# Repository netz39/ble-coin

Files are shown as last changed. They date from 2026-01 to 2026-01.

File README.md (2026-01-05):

# BLE Keyfob Authentication (PROJECT STATUS: DEPLOYED)
The purpose of this project is to provide members of the [NETZ39 Hackerspace](http://www.netz39.de/) a new, (sufficiently) secure and easy-to-use way to unlock the door of the Hackerspace.

## Principle Structure
This project uses Bluetooth Low Energy 5 as a wireless transport. An [**authenticated**, **encrypted**](https://en.wikipedia.org/wiki/CCM_mode) and [**private**](https://www.bluetooth.com/blog/bluetooth-technology-protecting-your-privacy/) connection is used with security mode 1 level 4. On top of BLE security, a simple [MAC based challenge-response authentication](https://crypto.stackexchange.com/questions/51931/hmac-based-challenge-response-authentication) using the [BLAKE2s hash function](https://blake2.net/) in MAC mode is used.

Components:
* A central (base station) with a NRF52480 chip, here a [**NRF52840 dongle**](https://www.nordicsemi.com/?sc_itemid=%7BCDCCA013-FE4C-4655-B20C-1557AB6568C9%7D)


* Peripherals (key fobs) using an NRF52832 chip, here a [**chinese board**](https://www.aliexpress.com/item/32954025507.html)


Both types of devices use the [Zephyr OS with integrated BLE stack](https://www.zephyrproject.org/).

**No real pairing** is done with devices in this project.
Pairing and bonding is done at when flashing a coin. This step generates the BLE address and keys (IRK, LTK) and the key for application-layer security (SPACEKEY). There is a shell interface at the central to list, add and remove coins.

The central continuously scans for known devices. Upon connection, it immediately tries to turn on encryption and kills the connection if that fails.

The peripherals implement the following GATT services:
nRF Connect screenshot

The spaceauth service expects a full BLAKE2s block (64B) of data to be sent to the challenge characteristic. Writing to this characteristic is protected and only available with a valid BLE bond.
After the challenge has been received, a response (32B) is generated. The first few bytes of the response (as much as fits one MTU) are then **indicated** to the central.

After that, the central knows it can download the response. The response is then checked with the locally generated response with **constant time comparison**.

The peripherals shut down when a connection to them is cancelled. They start up again when the button is pressed.
Both peripherals and the central kill the connection after a short timeout (5s).

## Building locally (on Linux)
1. Follow the [installation instructions](https://github.com/zephyrproject-rtos/zephyr/blob/master/doc/getting_started/installation_linux.rst) and install the Zephyr SDK (0.10.3) at the standard location (`/opt/zephyr-sdk/`).
2. Go to the `prod/` folder and run the `./bootstrap.sh` script.
3. Run `make` to build the projects.

## Building via Docker
1. Make sure you also cloned the submodules of this repository.
2. Make sure `docker` is installed and your account is in the `docker` group.
3. Inside the repository folder, execute `docker run -i -t -u $UID -v $(pwd):/data/build maz3max/coinbuild` to build using the [build image](https://github.com/maz3max/ble-coin-docker).

## How to use?
1. Use the `gen_bond.py` script in the `prod/` folder to generate a `central.txt` and a `coins.txt` file. It will also generate a hex-file for the specific coin containing the keys (e.g. `coin_d33efc87ed2e.hex`). Every coin gets a line in `coins.txt`.
5. Flash `coin_[a-f0-9]{12}\.hex` onto the coin.
6. Flash `central.hex` onto the dongle. Connect to its USB Serial with Baudrate 115200 (on Linux, it is something like this`/dev/serial/by-id/usb-ZEPHYR_N39_BLE_KEYKEEPER_0.01-if00`)
7. Press enter to make sure you are in the shell
8. use the `central_setup` command with the contents of your `central.txt` to initialize the address and the IRK of the central.
9. use the `coin add` command with the last line of your `coins.txt` to add the newly compiled coin.
10. `reboot` if you like and run `ble_start` to start searching for devices.

## Basic Authentication Sequence
sequence diagram

## Caveats
* Only **symmetrical** keys are used.
* The **authenticated pairing** part of the BLE security becomes obsolete because it only refers to pairing which is done via preprogramming here.
* Denial of Service cannot easily be cancelled out when using BLE.
* Like legacy-keys made out of metal, one of the BLE keys could be stolen and misused. (Authentication by ownership)
* Parts are not super-cheap: The central costs 10€ and one keyfob cost 5.50€
* NRF52 Access Port Protection is broken: https://limitedresults.com/2020/06/nrf52-debug-resurrection-approtect-bypass/

## FAQ
* Why BLE?
    * the transport had to be wireless, low power and provide connection-level security
    * standardized and widespread technology allows to replace parts of the system easily
* Why Zephyr?
    * very active & helpful community
    * Open-Source BLE Stack
    * supports CMake
    * build system less annoying than Apache Mynewt
* Why not use the cheaper NRF51822?
    * AFAIK this chip does not have enough flash to support the Zephyr BLE stack with enabled security
    * The flash read back protection is also broken: [step-by-step guide](https://www.pentestpartners.com/security-blog/nrf51822-code-readout-protection-bypass-a-how-to/)
* How do I get the software onto the devices?
    * For the NRF52840 dongle, you can use [nRF Connect for Desktop](https://www.nordicsemi.com/Software-and-Tools/Development-Tools/nRF-Connect-for-desktop)
    * For the coins, you have to use a Serial-Wire-Debug Programmer, but a [cheap 2€ STLinkV2 clone](https://de.aliexpress.com/item/32792513237.html) will do just fine using [OpenOCD](http://openocd.org/), See [coin readme](./coin/README.md)
* Can I use this project for my own purposes?
    * See LICENSE.md

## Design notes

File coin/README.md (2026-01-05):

# Coin Firmware
This directory contains the firmware that creates a **BLE peripheral** loading the **BLE bond** and the **SPACEKEY** from flash using zephyr's settings API.

## Usage
Please refer to the top level README file for flashing instructions. Especially, this firmware will **not** work properly when flashed onto a virgin, mass-erased chip, because the **settings partition** needs to be flashed too.

Flashing can be done [using a BlackMagic Probe](https://github.com/blacksphere/blackmagic/wiki) or [using an STLinkV2 with OpenOCD](https://medium.com/@ly.lee/coding-nrf52-with-rust-and-apache-mynewt-on-visual-studio-code-9521bcba6004) or [using a Raspberry Pi Zero W and a flashing jig](../flashing-jig/README.md).

Please note that you will not be able to lift the **Access Port Protection** with an STLinkV2. That means the coins are **locked down** from flashing until you get another flash tool. Don't worry - some STLinkV2 clones can be turned into BlackMagic Probes if they have sufficient (128K) flash. You could also buy a real BlackMagic Probe, an FT2232H breakout board or a SEGGER JLink. It is possible to [remove the nRF52 Flash Protection with a Raspberry Pi](https://medium.com/@ly.lee/coding-nrf52-with-rust-and-apache-mynewt-on-visual-studio-code-9521bcba6004).

When flashed, press the button on the coin to wake it up. The LED will light up and the coin will send **BLE advertisements** to the central signaling that it wants to connect. The LED starts flashing when the coin finds its central.

When finished authenticating, on connection loss or when a timeout of 10s is triggered, the coin goes into **deep sleep mode**.

## Code Structure
The code is structured in 4 parts:
* `bas`: contains ADC boilerplate code and GATT Battery Service
* `io`: contains LED (blinking) and Button handling
* `spaceauth`: registers settings handler for loading the **SPACEKEY** and the **custom GATT Spaceauth Service** that uses the [BLAKE2s hash function](https://blake2.net/) to implement a challenge-response authentication
* `main`: handles the connection and power management while (obviously) containing the main function

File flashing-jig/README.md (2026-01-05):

# Flashing BLE Coins with a RPi Zero W 1

The coin is connected using a programming jig
that controls power output with a transistor (active-low).

flashing jig

A red LED lights up when the coin is powered.
flashing jig powered

CAD files can be found in the `cad/` folder.
The PCB is not strictly necessary, you can wire it up with just pogo pins and some glue. Having a transistor to control power is recommended though.

The following pins are used:

* 3.3V
* GND
* swclk = GPIO 11
* swdio = GPIO 25
* pwr_en = GPIO 27

The `openocd` package needs to be installed for this to work. A special version configured with `--enable-bcm2835gpio --enable-sysfsgpio` is needed for bitbanging on the RPi GPIO pins.

The `ble_gen_coin.py <name>` script generates a hex file for flashing. A list of coins and names is maintained in `coins.txt` and `names.txt`. The format is compatible with [ble-keykeeper](https://github.com/netz39/ble-keykeeper-role/blob/main/templates/ble_keykeeper.py).

While flashing, the coins are put in a protected mode. You can query that mode with `./check.sh` and factory-reset a coin with `./unlock.sh`.

Flashing is done with `./flash.sh something.hex`.

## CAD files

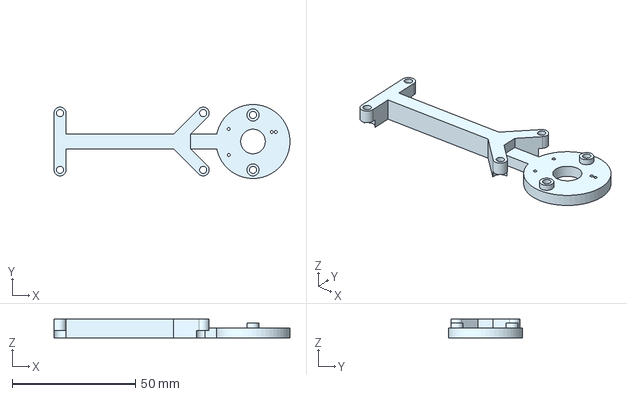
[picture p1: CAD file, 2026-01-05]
flashing-jig/CAD/stand.step
95.6 x 30.0 x 7.60 mm

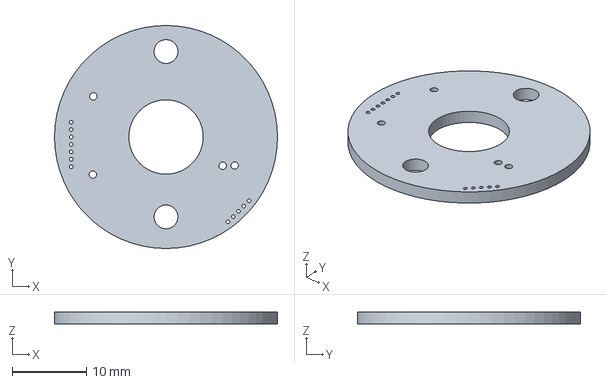
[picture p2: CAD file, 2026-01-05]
flashing-jig/CAD/PCB.step
30.0 x 30.0 x 1.60 mm

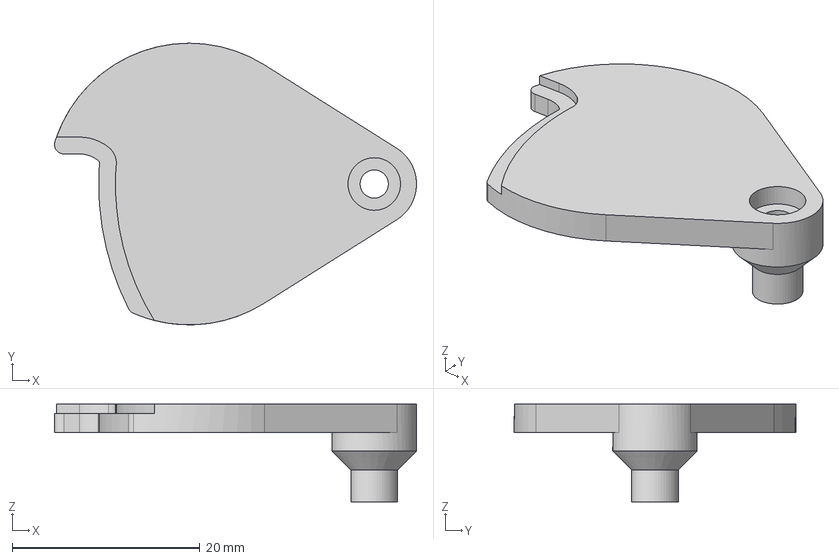
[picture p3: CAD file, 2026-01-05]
flashing-jig/CAD/lid.step
38.6 x 30.0 x 10.4 mm

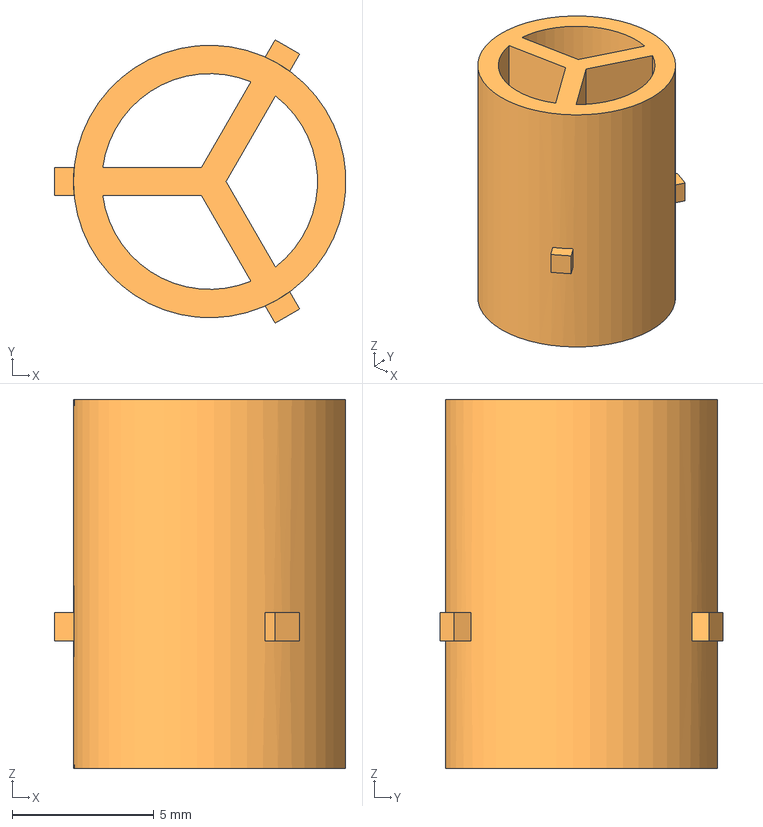
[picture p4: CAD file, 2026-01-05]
flashing-jig/CAD/button-extender.step
10.3 x 9.98 x 13.0 mm

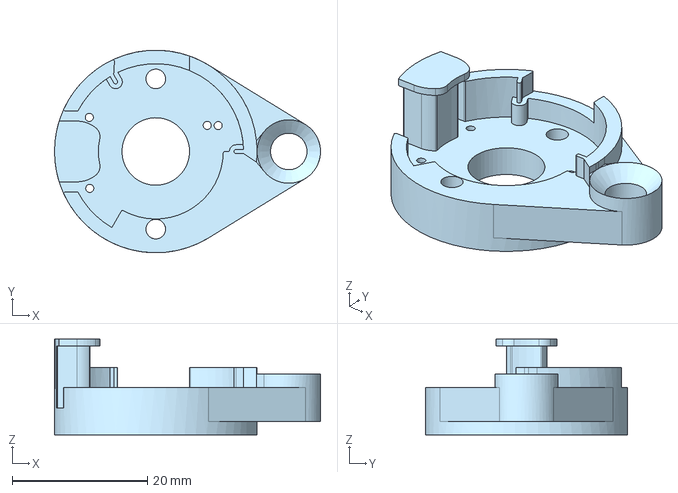
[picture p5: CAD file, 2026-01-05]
flashing-jig/CAD/base.step
39.4 x 30.0 x 14.2 mm

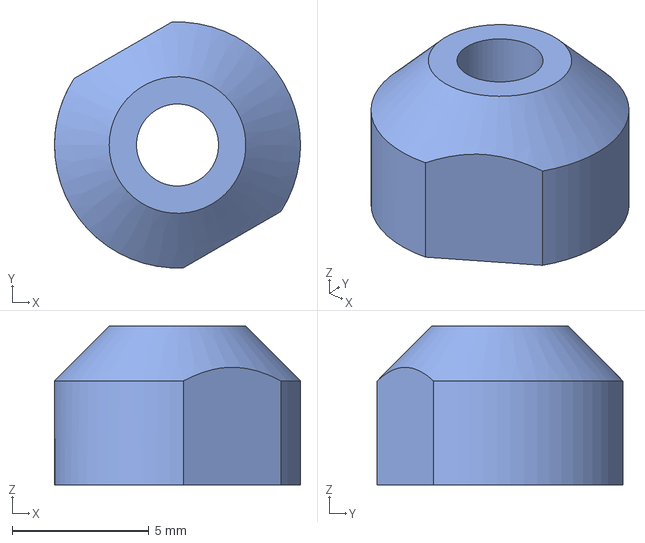
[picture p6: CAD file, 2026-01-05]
flashing-jig/CAD/nut.step
9.00 x 8.99 x 5.80 mm
